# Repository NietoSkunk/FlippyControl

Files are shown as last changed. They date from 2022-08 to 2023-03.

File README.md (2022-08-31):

# FlippyControl

Arduino / ESP32 Shield for controlling the [Luminator MAX3000](https://github.com/NietoSkunk/FlippyDriver) Flip Dot driver.

In addition to connecting the appropriate pins of the microcontroller to the data harness, it also includes pads to connect two Wii Extension Controllers (including Classic Controller, Pro Controller, etc), a USB-C 5V power input, and selectable Vcc outputs.

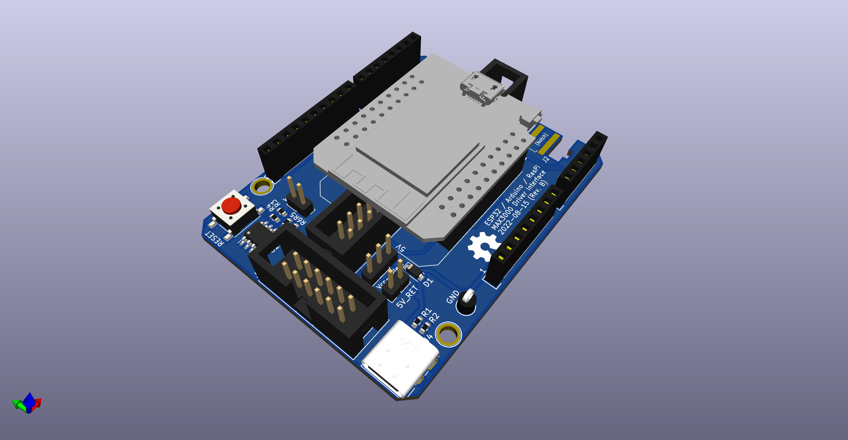
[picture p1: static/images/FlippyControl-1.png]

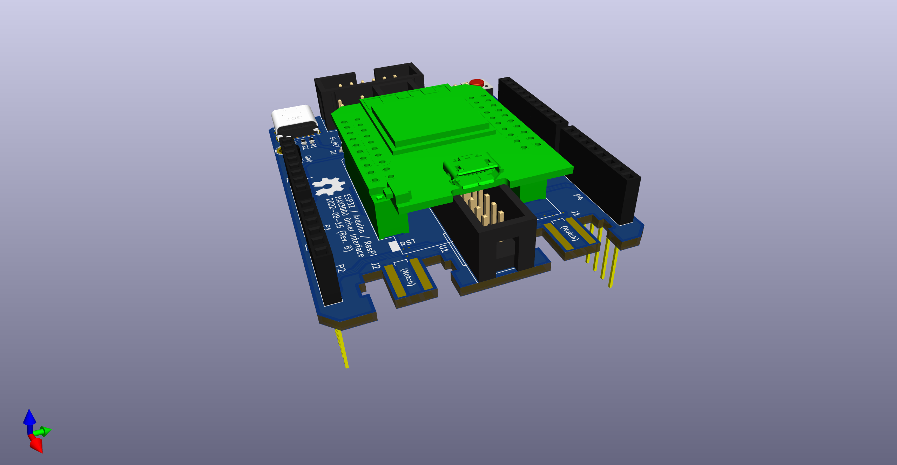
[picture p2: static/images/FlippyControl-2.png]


## Cloning repository (with Submodules)

```bash
$ git clone --recurse-submodules git@github.com:NietoSkunk/FlippyControl.git
```

## Production notes

* Only one MCU should be connected at a time.

## Data Harness

| Pin | # | # | Pin |
| --- | - | - | --- |
| VCC | 1 | 2 | GND |
| MOSI | 3 | 4 | PULSE_ENABLE |
| LATCH | 5 | 6 | COL_PULSE_N |
| CLK | 7 | 8 | ROW_PULSE_N |
| RESET | 9 | 10 | LED PWM |
| 5V Return | 11 | 12 | GND |

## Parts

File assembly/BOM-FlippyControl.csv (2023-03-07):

Comment | Designator | Footprint | LCSC
GND | TP7 | TestPoint_Keystone_5005-5009_Compact
ESP32-D1-Mini | U1 | ESP32_mini
Power | P1 | Socket_Strip_Arduino_1x08
Analog | P2 | Socket_Strip_Arduino_1x06
Digital | P3 | Socket_Strip_Arduino_1x10
Digital | P4 | Socket_Strip_Arduino_1x08
CONN_01X01 | P5 | Arduino_1pin
CONN_01X01 | P7 | Arduino_1pin
PMEG60T10ELR | D1 | D_SOD-123
USB4085-GF-A | J4 | USB_C_Receptacle_GCT_USB4085
Data Harness Out | J3 | IDC-Header_2x06_P2.54mm_Vertical
Vcc-Select | JP1 | PinHeader_1x03_P2.54mm_Vertical
5.1k | R2 | R_0603_1608Metric
5.1k | R1 | R_0603_1608Metric
DNP | R3 | R_0603_1608Metric
10K | R4 | R_0603_1608Metric
RESET | SW1 | SW_SPST_PTS645
5V_RET | JP2 | PinHeader_1x02_P2.54mm_Vertical
WP | J6 | PinHeader_1x02_P2.54mm_Vertical
3.9k | R5 | R_0603_1608Metric
RasPI-40Pin | J5 | IDC-Header_2x20_P2.54mm_Vertical
3.9k | R6 | R_0603_1608Metric
CAT24C32 | U2 | SOIC-8_3.9x4.9mm_P1.27mm
4.7k | R12 | R_0603_1608Metric
4.7k | R11 | R_0603_1608Metric
4.7k | R10 | R_0603_1608Metric
4.7k | R9 | R_0603_1608Metric
4.7k | R8 | R_0603_1608Metric
4.7k | R7 | R_0603_1608Metric

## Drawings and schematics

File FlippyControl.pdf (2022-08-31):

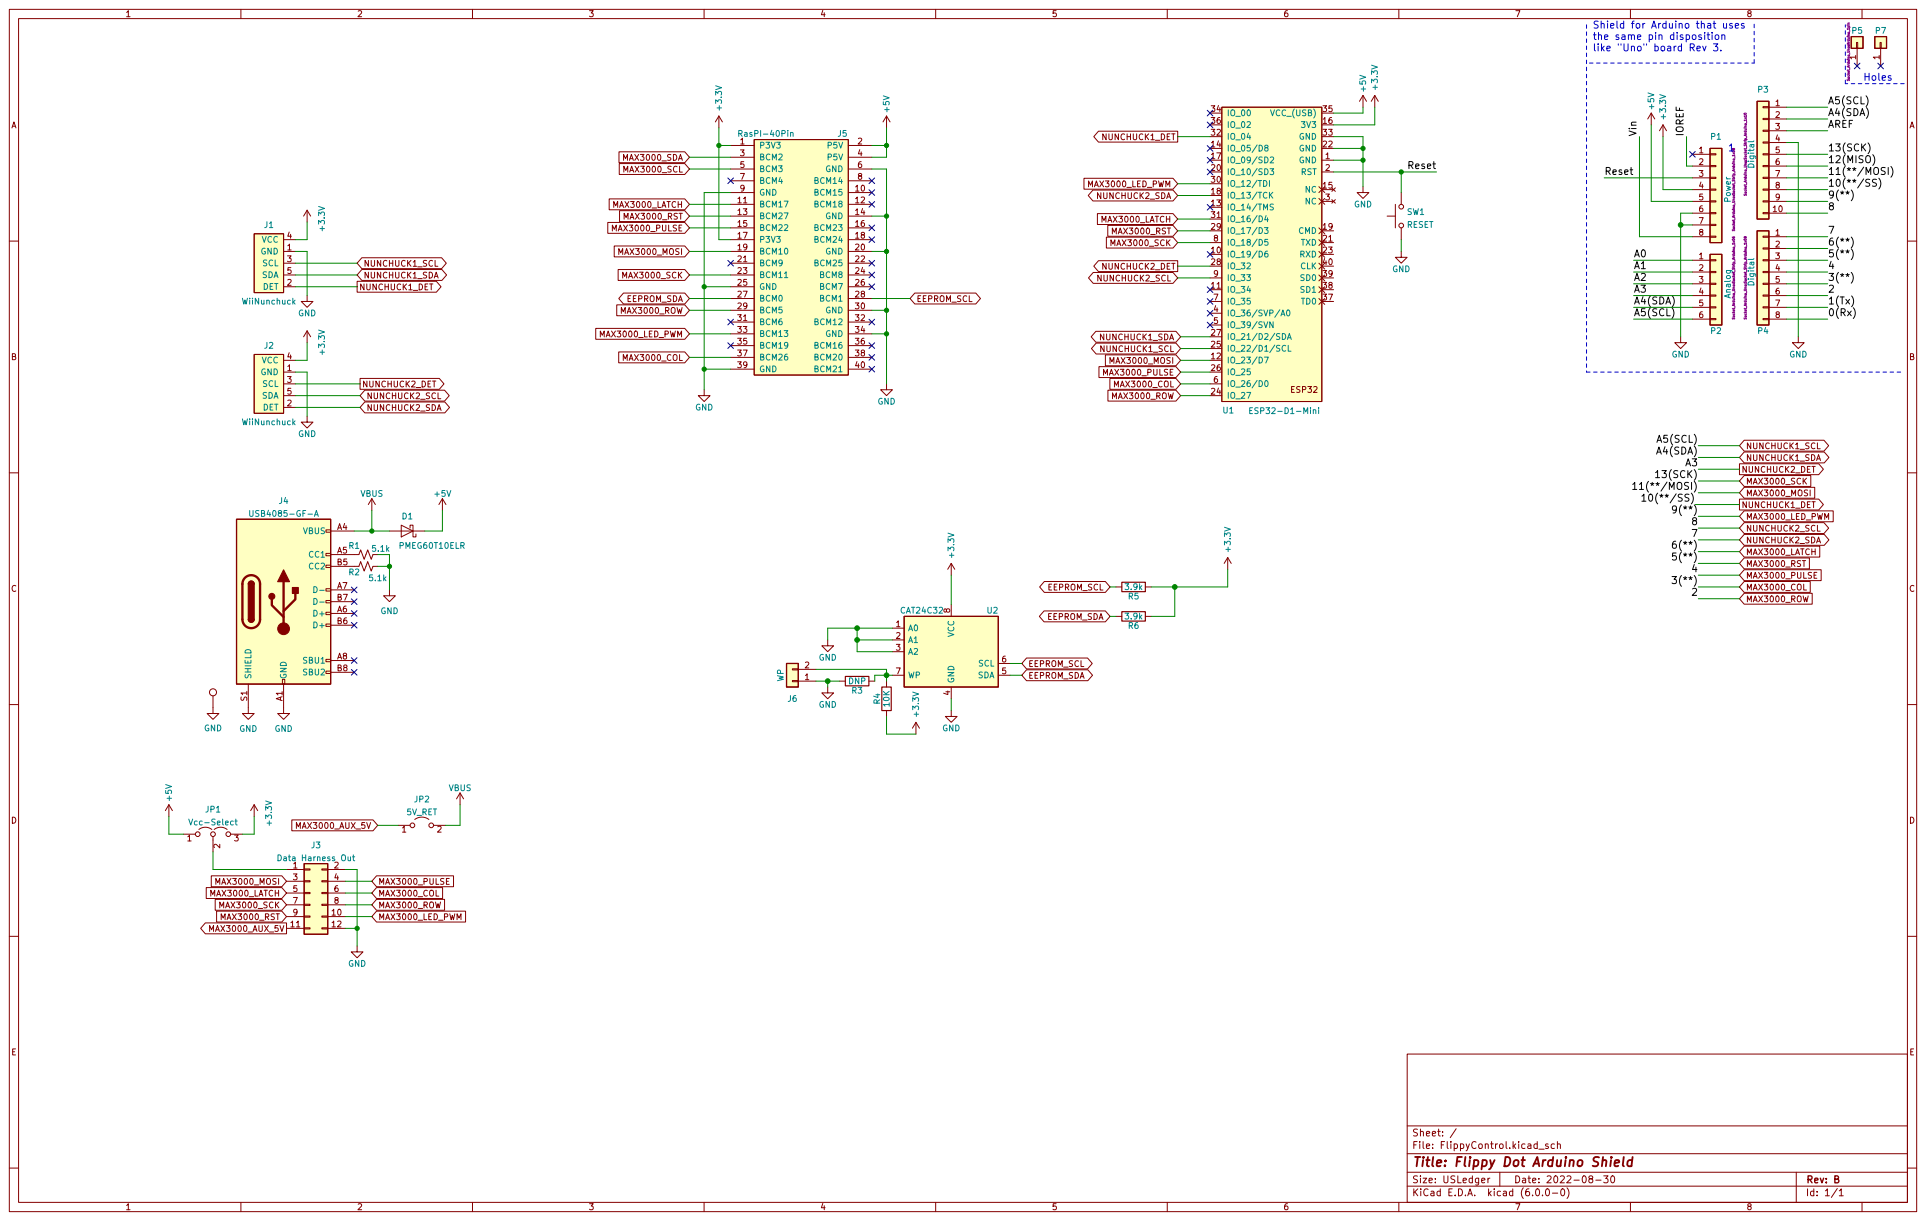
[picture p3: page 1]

the same pin disposition

Id: 1/1 Title: Flippy Dot Arduino Shield

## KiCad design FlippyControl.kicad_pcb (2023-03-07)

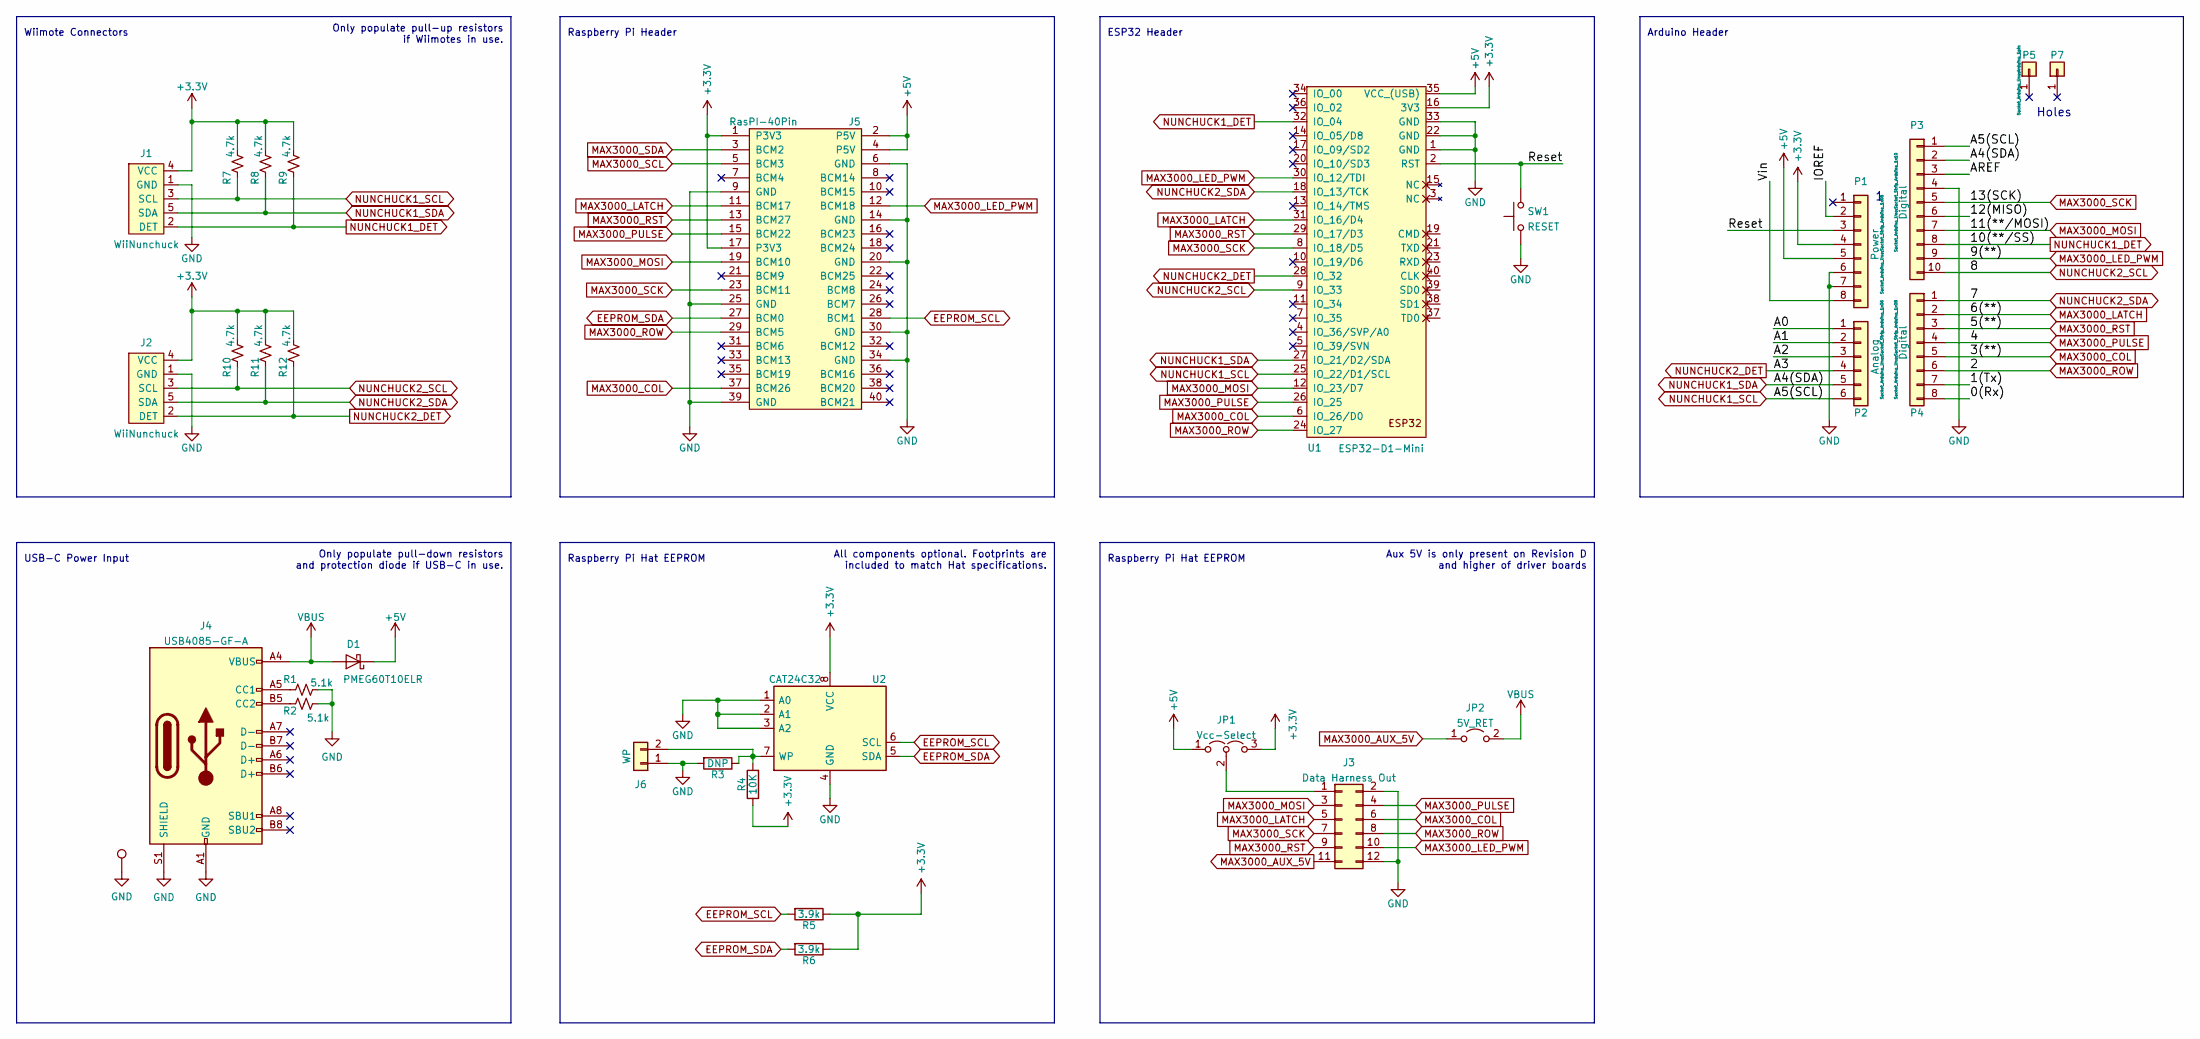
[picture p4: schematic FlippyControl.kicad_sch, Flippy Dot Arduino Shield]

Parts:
D1: PMEG60T10ELR; D_SOD-123
J1, J2: WiiNunchuck
J3: Data Harness Out; IDC-Header_2x06_P2.54mm_Vertical
J4: USB4085-GF-A; USB_C_Receptacle_GCT_USB4085
J5: RasPI-40Pin; IDC-Header_2x20_P2.54mm_Vertical
J6: WP; PinHeader_1x02_P2.54mm_Vertical
JP1: Vcc-Select; PinHeader_1x03_P2.54mm_Vertical
JP2: 5V_RET; PinHeader_1x02_P2.54mm_Vertical
P1: Power; Socket_Strip_Arduino_1x08
P2: Analog; Socket_Strip_Arduino_1x06
P3: Digital; Socket_Strip_Arduino_1x10
P4: Digital; Socket_Strip_Arduino_1x08
P5, P7: CONN_01X01; Arduino_1pin
R1, R2: 5.1k; R_0603_1608Metric
R3: DNP; R_0603_1608Metric
R4: 10K; R_0603_1608Metric
R5, R6: 3.9k; R_0603_1608Metric
R7, R8, R9, R10, R11, R12: 4.7k; R_0603_1608Metric
SW1: RESET; SW_SPST_PTS645
TP7: GND; TestPoint_Keystone_5005-5009_Compact
U1: ESP32-D1-Mini; ESP32_mini
U2: CAT24C32; SOIC-8_3.9x4.9mm_P1.27mm

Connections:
+3V3: J1.4 (VCC), J2.4 (VCC), J5.1 (P3V3), J5.17 (P3V3), JP1.3 (B), P1.4, R4.1, R5.1, R6.1, R7.2, R8.2, R9.2, R10.2, R11.2, R12.2, U1.16 (3V3), U2.8 (VCC)
+5V: D1.1 (K), J5.2 (P5V), J5.4 (P5V), JP1.1 (A), P1.5, U1.35 (VCC_(USB))
/0(Rx): P4.8
/1(Tx): P4.7
/12(MISO): P3.6
/A0: P2.1
/A1: P2.2
/A2: P2.3
/AREF: P3.3
/IOREF: P1.2
/Reset: P1.3, SW1.2, U1.2 (RST)
/Vin: P1.8
EEPROM_SCL: J5.28 (BCM1), R5.2, U2.6 (SCL)
EEPROM_SDA: J5.27 (BCM0), R6.2, U2.5 (SDA)
GND: J1.1 (GND), J2.1 (GND), J3.2, J3.12, J4.A1 (GND), J4.A12 (GND), J4.B1 (GND), J4.B12 (GND), J4.S1 (SHIELD), J5.6 (GND), J5.9 (GND), J5.14 (GND), J5.20 (GND), J5.25 (GND), J5.30 (GND), J5.34 (GND), J5.39 (GND), J6.1, P1.6, P1.7, P3.4, R1.2, R2.2, R3.2, SW1.1, TP7.1, U1.1 (GND), U1.22 (GND), U1.33 (GND), U2.1 (A0), U2.2 (A1), U2.3 (A2), U2.4 (GND)
MAX3000_AUX_5V: J3.11, JP2.1 (A)
MAX3000_COL: J3.6, J5.37 (BCM26), P4.5, U1.6 (IO_26/D0)
MAX3000_LATCH: J3.5, J5.11 (BCM17), P4.2, U1.31 (IO_16/D4)
MAX3000_LED_PWM: J3.10, J5.12 (BCM18), P3.9, U1.30 (IO_12/TDI)
MAX3000_MOSI: J3.3, J5.19 (BCM10), P3.7, U1.12 (IO_23/D7)
MAX3000_PULSE: J3.4, J5.15 (BCM22), P4.4, U1.26 (IO_25)
MAX3000_ROW: J3.8, J5.29 (BCM5), P4.6, U1.24 (IO_27)
MAX3000_RST: J3.9, J5.13 (BCM27), P4.3, U1.29 (IO_17/D3)
MAX3000_SCK: J3.7, J5.23 (BCM11), P3.5, U1.8 (IO_18/D5)
MAX3000_SCL: J5.5 (BCM3)
MAX3000_SDA: J5.3 (BCM2)
NUNCHUCK1_DET: J1.2 (DET), P3.8, R9.1, U1.32 (IO_04)
NUNCHUCK1_SCL: J1.3 (SCL), P2.6, P3.1, R7.1, U1.25 (IO_22/D1/SCL)
NUNCHUCK1_SDA: J1.5 (SDA), P2.5, P3.2, R8.1, U1.27 (IO_21/D2/SDA)
NUNCHUCK2_DET: J2.2 (DET), P2.4, R12.1, U1.28 (IO_32)
NUNCHUCK2_SCL: J2.3 (SCL), P3.10, R10.1, U1.9 (IO_33)
NUNCHUCK2_SDA: J2.5 (SDA), P4.1, R11.1, U1.18 (IO_13/TCK)
unnamed: J3.1, JP1.2 (C)
unnamed: J4.A5 (CC1), R1.1
unnamed: J4.B5 (CC2), R2.1
unnamed: J6.2, R3.1, R4.2, U2.7 (WP)
VBUS: D1.2 (A), J4.A4 (VBUS), J4.A9 (VBUS), J4.B4 (VBUS), J4.B9 (VBUS), JP2.2 (B)

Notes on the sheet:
All components optional. Footprints are included to match Hat specifications.
Aux 5V is only present on Revision D and higher of driver boards
Only populate pull-up resistors if Wiimotes in use.
Raspberry Pi Hat EEPROM
ESP32 Header
Raspberry Pi Header
Holes
Wiimote Connectors
Only populate pull-down resistors and protection diode if USB-C in use.
USB-C Power Input
Arduino Header

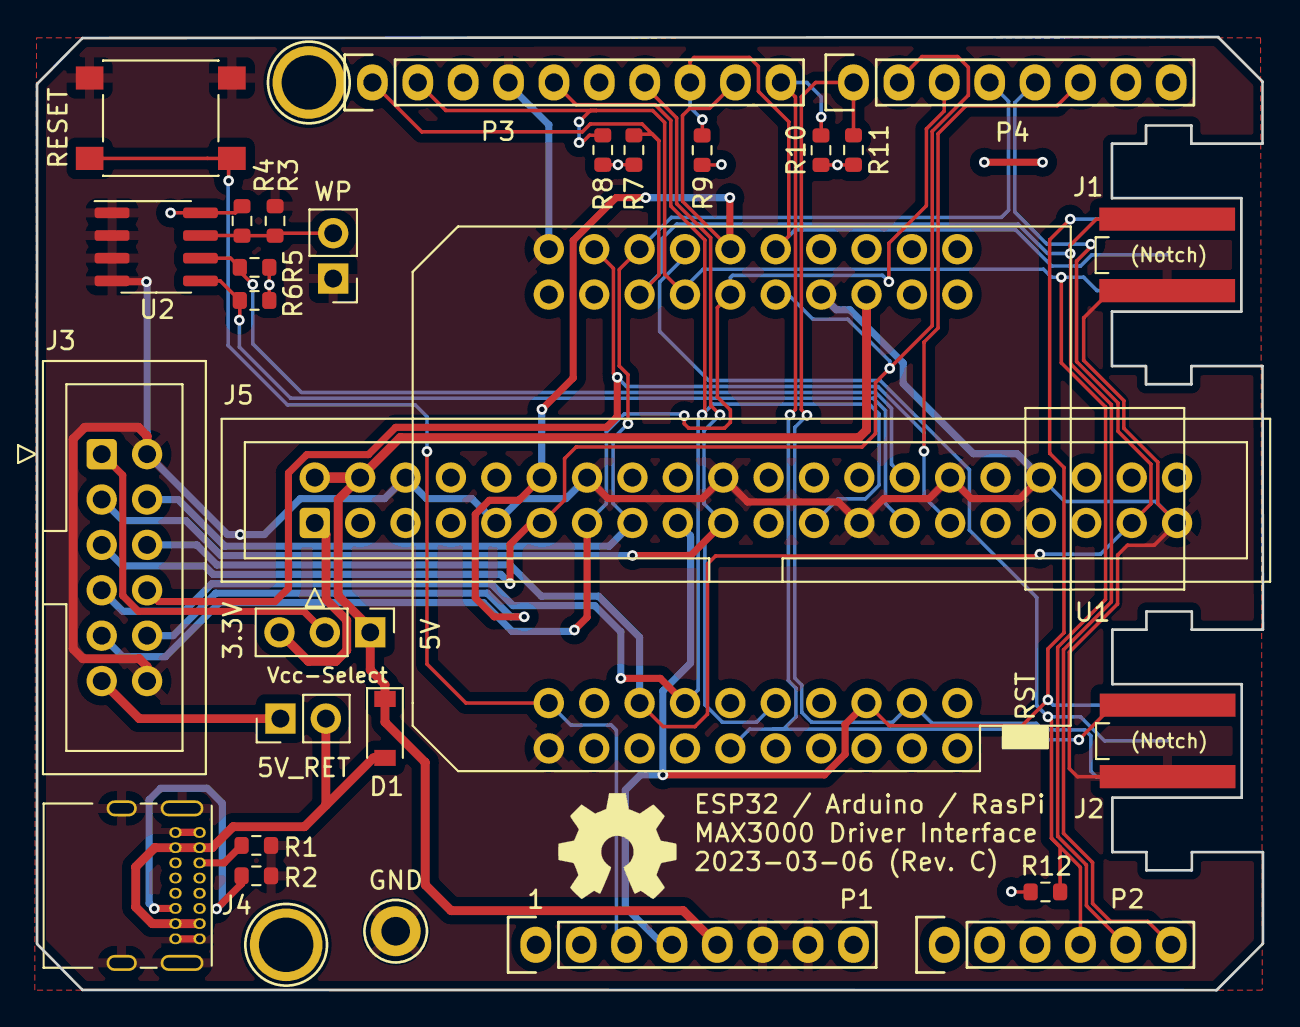
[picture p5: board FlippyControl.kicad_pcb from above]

Board: 2 copper layers, 68.6 x 53.3 mm, 31 parts (0 on the bottom side), 26 nets.

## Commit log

2022-08-17 Initial revision of FlippyControl
    [FlippyControl-CuBottom.gbr, FlippyControl-CuTop.gbr, FlippyControl-EdgeCuts.gbr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]
2022-08-17 Add missing Schematic PDF
2022-08-25 Add submodule and migrate project
    [BOM-FlippyControl.csv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]
2022-08-31 Final Rev.B, adding RasPi connector and PWM output
    [BOM-FlippyControl.csv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]
2023-03-07 Add pullups, fix miswired pads
    [BOM-FlippyControl.csv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]
